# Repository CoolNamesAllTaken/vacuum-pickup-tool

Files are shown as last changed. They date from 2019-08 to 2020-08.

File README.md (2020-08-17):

# vacuum-pickup-tool
Vacuum pickup tool for building SMT boards.

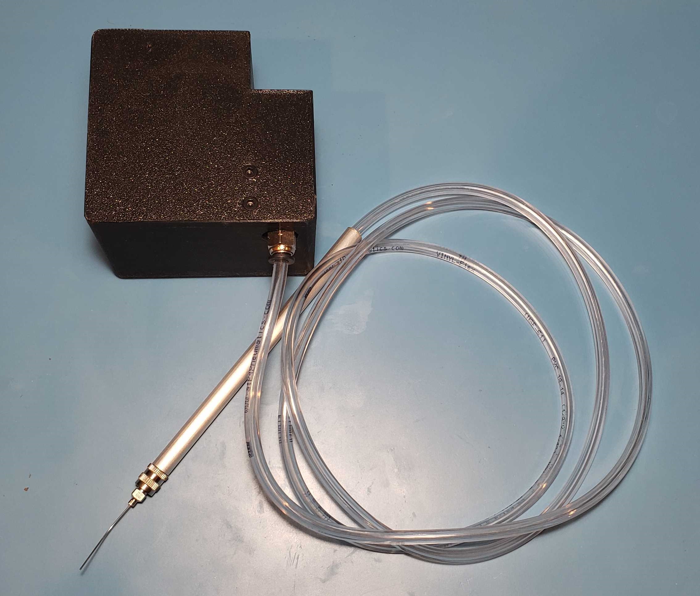
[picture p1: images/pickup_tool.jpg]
Image of fully assembled system


## Overview and Description
The Vacuum Pickup Tool is designed to facilitate manual pick-and-place of SMD components onto PCBs, offering faster cycle time than tweezers, since components can be picked directly from their tape.
It consists of a 3d printed case (powered by a 12V barrel jack), a foot pedal (connected to the case by way of a 3.5mm audio cable), and the tool itself (connected to the case by a PVC vacuum tubing).
The "pencil" terminates in a [Luer lock connector](https://en.wikipedia.org/wiki/Luer_taper), a common standard for affixing needles to syringes.

## Parts List
* 1x [12V NC Solenoid Valve](https://www.amazon.com/gp/product/B07BGXMG7H)
* 1x [12V Brushless Vacuum Pump](https://www.ebay.com/itm/US-Stock-Parker-12V-Brushless-Dual-Head-Vacuum-Pump-Diaphragm-Pump-DIY-Air-Pump/392156385546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)
* 1x [Male Luer Lock to 3mm or 1/8" Hose Barb Adapter](https://www.ebay.com/itm/Metal-Male-Luer-Lock-Syringe-Fitting-to-3mm-or-1-8-Barb-Hose-ID-43/202463602776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)
* 1x [1/6" Hose Barb Tee Fitting](https://www.amazon.com/gp/product/B017UXJ3VG)
* 1x [3/8in Diameter x 12in Aluminum Tube](https://www.ebay.com/itm/K-S-3-8-in-Dia-x-12-in-L-Aluminum-Tube-Round-/383055055746?hash=item592fdc4b82)
* 1x [12V 2-Position 3-Way Solenoid Valve](https://www.amazon.com/uxcell-Miniature-Solenoid-Valve-Positions/dp/B07WS93PCV)
* 1x [12V 1A Power Supply](https://www.amazon.com/gp/product/B00FEOB4EI)
* 1x [Push to Connect Air Hose Fitting](https://www.amazon.com/gp/product/B07H8KPL2W)
* 1x [1/8" ID 1/4" OD Vinyl-Flex Tubing](https://www.amazon.com/gp/product/B00E6BCV0G/ref=ppx_yo_dt_b_asin_title_o01_s02?ie=UTF8&psc=1)
* 1x [Momentary Foot Switch Pedal](https://www.amazon.com/Linemaster-T-91-S-Treadlite-Electrical-Momentary/dp/B002P4XREA)
* 1x [Male to Male 8ft 1/8" Stereo Audio Cable](https://www.amazon.com/AmazonBasics-Stereo-Audio-Cable-Meters/dp/B00NO73Q84)
* 1x [Arduino Nano Clone](https://www.amazon.com/ELEGOO-Arduino-ATmega328P-Without-Compatible/dp/B0713XK923)
* 1x [Adjustable Buck Converter](https://www.amazon.com/Ultra-MP1584EN-Converter-Adjustable-Module/dp/B07SJFTD7F)
* 1x [12V 1A Power Supply (5.5x2.1mm Barrel Jack)](https://www.amazon.com/gp/product/B00FEOB4EI)

## Important Note
The pictures are of an older version of this tool, which has a slightly different PCB that required some extra wire finagling. The air cabling is exactly the same, as are the placements of each part.

## Step 1: Assemble and mount the PCB:
1. Solder all surface mount componenets. In general, going from smallest to largest is advisable so you don't have larger componenets blocking your iron's access to smaller nearby pads.
Keep in mind that diodes and LEDs have polarity! Refer to the pictures or the schematic to see the correct orientation.
2. Solder the male 2pos JST-PH connectors to the board, as well as the barrel jack. Be careful that the JST connectors are in the correct orientation (i.e. the red wire crimped in the female will correspond with the positive side when they are connected.)
3. Set the voltage output of the regulator. We used a bench power supply with alligator clips to supply 12V and a voltmeter with alligator clip leads to read the output voltage. Turn the on-board screw until the output is 5V. It is important to do this before the regulator and the Nano are soldered to the PCB, otherwise the regulator may provide a voltage that fries the Nano's 5V-tolerant pins before it is properly tuned.
4. Solder male headers on the Nano and the regulator. The easist way to get the headers straight up and aligned on the Nano is to place them in a breadboard. This will NOT work for the regulator, as the distances between its holes are inconsistent with a breadboard's.
5. Solder the Nano and regulator to the board.
6. Mount the PCB to the case with four M3 screws and nuts.
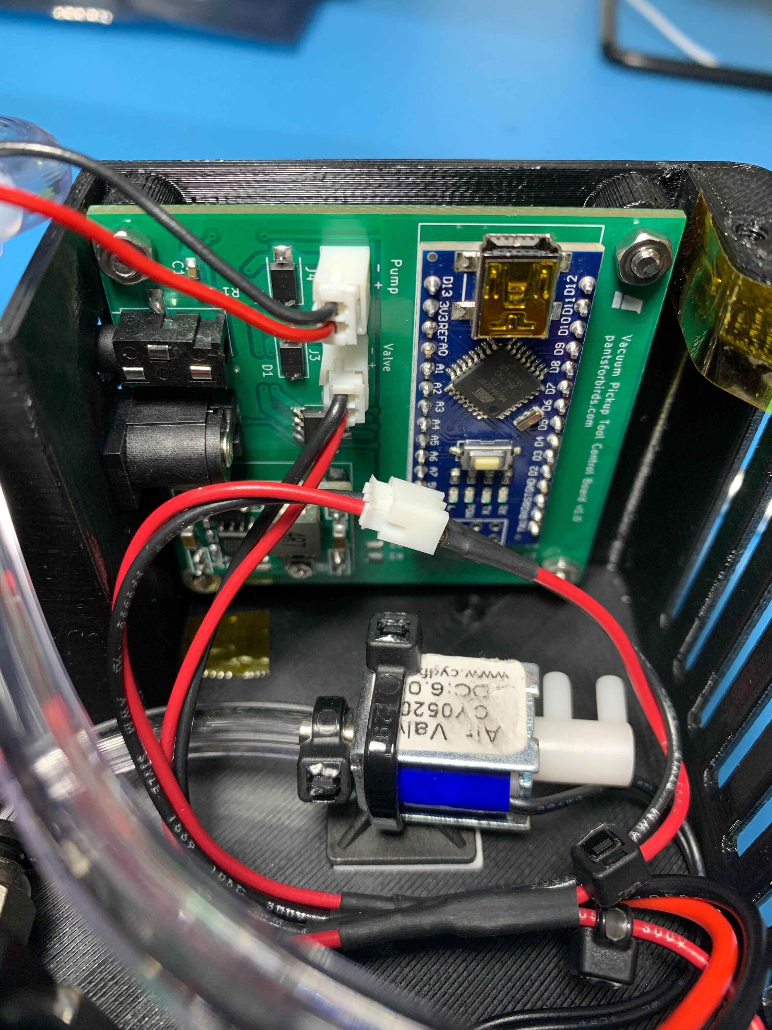
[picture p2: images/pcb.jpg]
Completed PCB


## Step 2: Connect the vacuum pump and solenoids:
1. Crimp and affix a female 2pos JST-PH connector to the leads of the vacuum pump. An Engineer PA-09 crimper can be used for this.
2. Crimp and affix a female 2pos JST-PH connector to the leads of each solenoid.
3. Remove the red "hats" from the vacuum pump.
4. Use two short M4 screws to affix the vacuum pump to the top plate of the case.
5. Place one square nut in each of the slots in each top corner of the case. 
6. Screw in a Push-to-Connect Tube Fitting to each of the three holes in the larger solenoid valve. Use a wrench to get them tight, but it is normal for 3ish threads to still extend outside of the hole when it is fully in.
9. Using the tubing and a T-fitting, connect the tubing as shown in the pictures. Leave enough "slack" so that the top (to which the vacuum pump is attached) can be removed without disconnecting the tubing.
8. Use 2 short M4 screws to affix the large solenoid to the bottom of the case.
9. Use a zip tie and a zip tie mount to affix the small solenoid to the bottom of the case.
10. Plug the female JST connectors into the PCB.
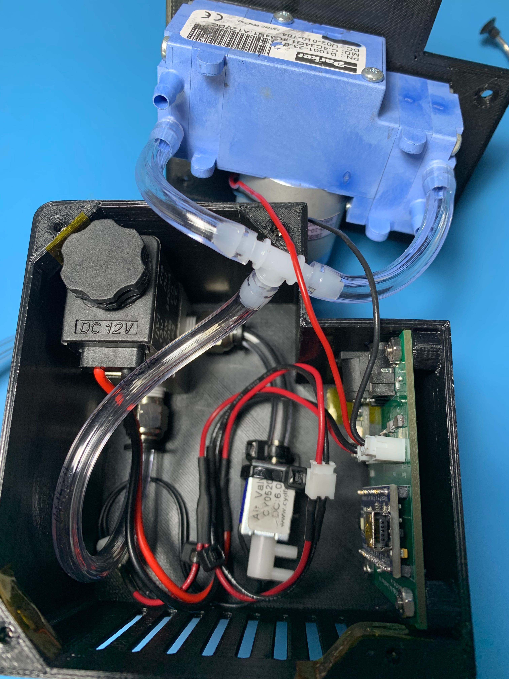
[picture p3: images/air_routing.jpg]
Vacuum pump and solenoids installed


## Step 3: Construct and connect the "pencil":
1. Cut the aluminum tube in half, since we want a 6in length. One way to cut it is by placing half in a vise and cutting with a hacksaw, then deburring and filing the rough edges.
2. Cut a long length of the vinyl tubing and feed it through the aluiminum tube.
3. Attach the Luer Lock adapter, and use Kapton tape to slightly increase the diameter of the front of the tube (over the Luer Lock adapter barb) until it makes a nice press fit into the tube.
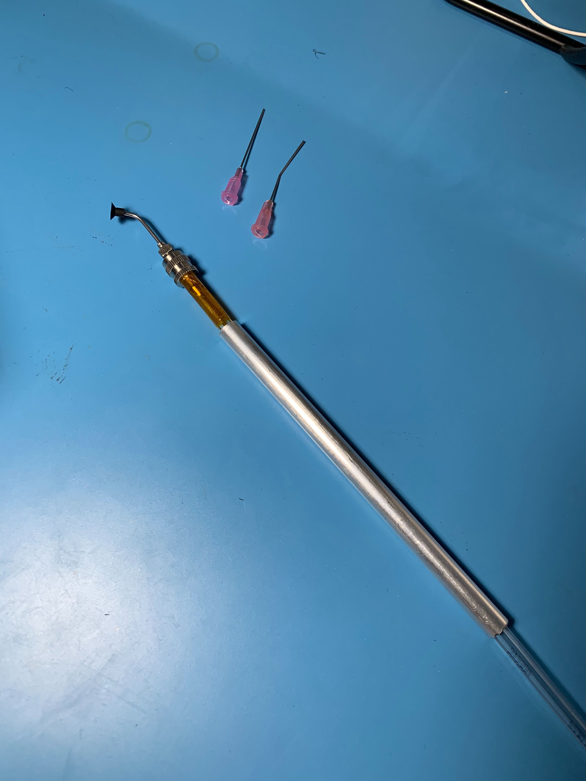
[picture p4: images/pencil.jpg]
Partially assembled pencil, showing Kapton tape that will create a press fit against the aluminum tube


## Step 4: Wire the foot pedal
1. Chop off the connector from one end of the 3.5mm audio cable. Strip ~1in of the outer cable insulation and ~0.3in of the insulation on each of the 3 inner cables.
2. Use a multimeter to map each internal cable to the sleeve, ring, and tip of the other end's connector. Chop off the wire corresponding to the sleeve; it is unneeded.
3. Unscrew the two side screws of the foot pedal to separate the two main pieces. Take out the plastic insert protecting the internal limit switch.
4. Loosen the two back screws to allow the cable through. Of the two remaining wires, solder one to the Common terminal of the limit switch, and the other to the Normally Open (NO) terminal. It may help to remove the limit switch when doing this. If you have the correct size of quick-connect spade terminals, these could be used to attach wires to the switch instead of soldering.
5. Replace the protective plastic, tighten the two back screws to provide strain relief on the incoming cable, then reattach the sides to each other with the side screws.

## Step 5: Build and flash the code:
1. Download and install Microsoft VSCode and the PlatformIO IDE extension following instructions [here](https://platformio.org/install/ide?install=vscode)
2. In the PlatformIO IDE, click Projects, then Add Existing, and navigate to the `src/vacuum_pickup_tool` directory.
3. In the terminal part of the IDE, run `platformio lib install PinChangeInterrupt`.
4. Plug in the Nano with a USB mini cable, and click the Upload arrow on the bottom bar.
5. If the Upload fails, it may be because different Nano clones use different bootloader versions. To try the other version, go to Projects then click the Configure button next to the Vacuum Pickup Tool project. Scroll down to board and change `nanoatmega328` to `nanoatmega328new`, then try again.

## Step 6: Putting it all together:
1. Plug in the 12V power, the audio cable, and the tubing from the "pencil".
2. When the power is inserted, red LEDs should be on inside the case. When the foot pedal is depressed, the vacuum will activate and a green LED should show inside the case.
3. After releasing the foot pedal, the green LED will turn off but the vacuum pump will remain on for a short period of time, so that if you're picking multiple parts in quick succession you don't have to wait for it to start up each time.

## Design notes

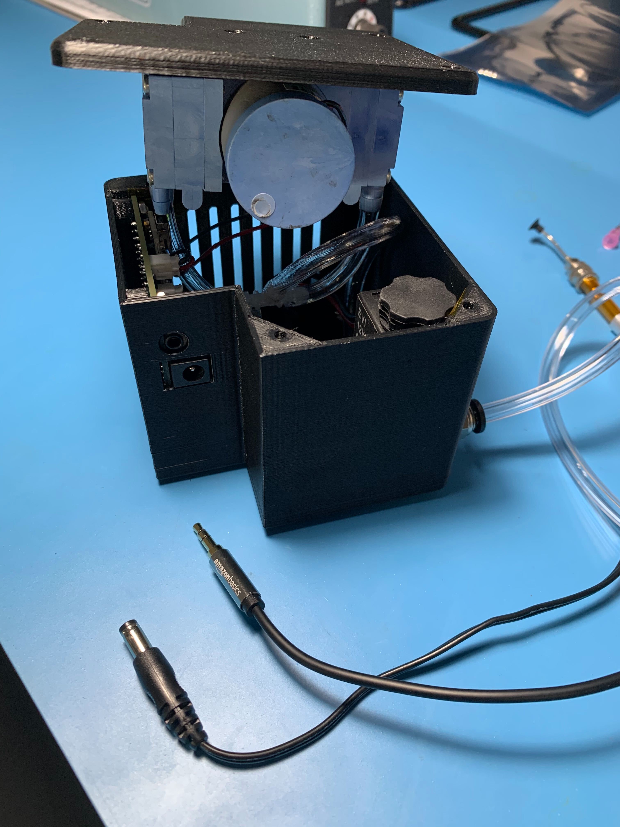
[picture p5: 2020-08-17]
images/power_and_trigger_inputs.jpg

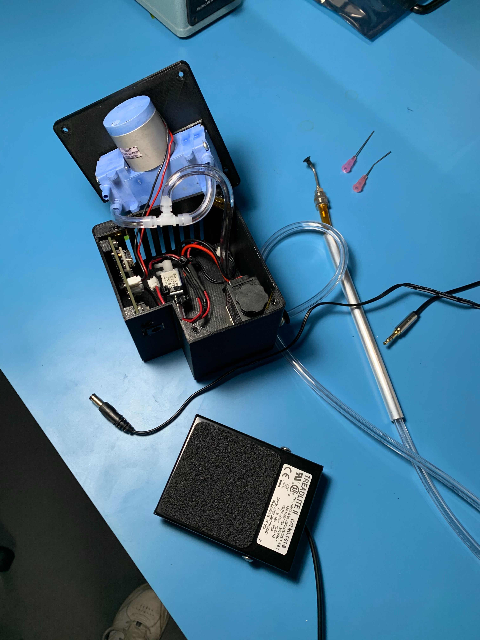
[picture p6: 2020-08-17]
images/entire_system.jpg

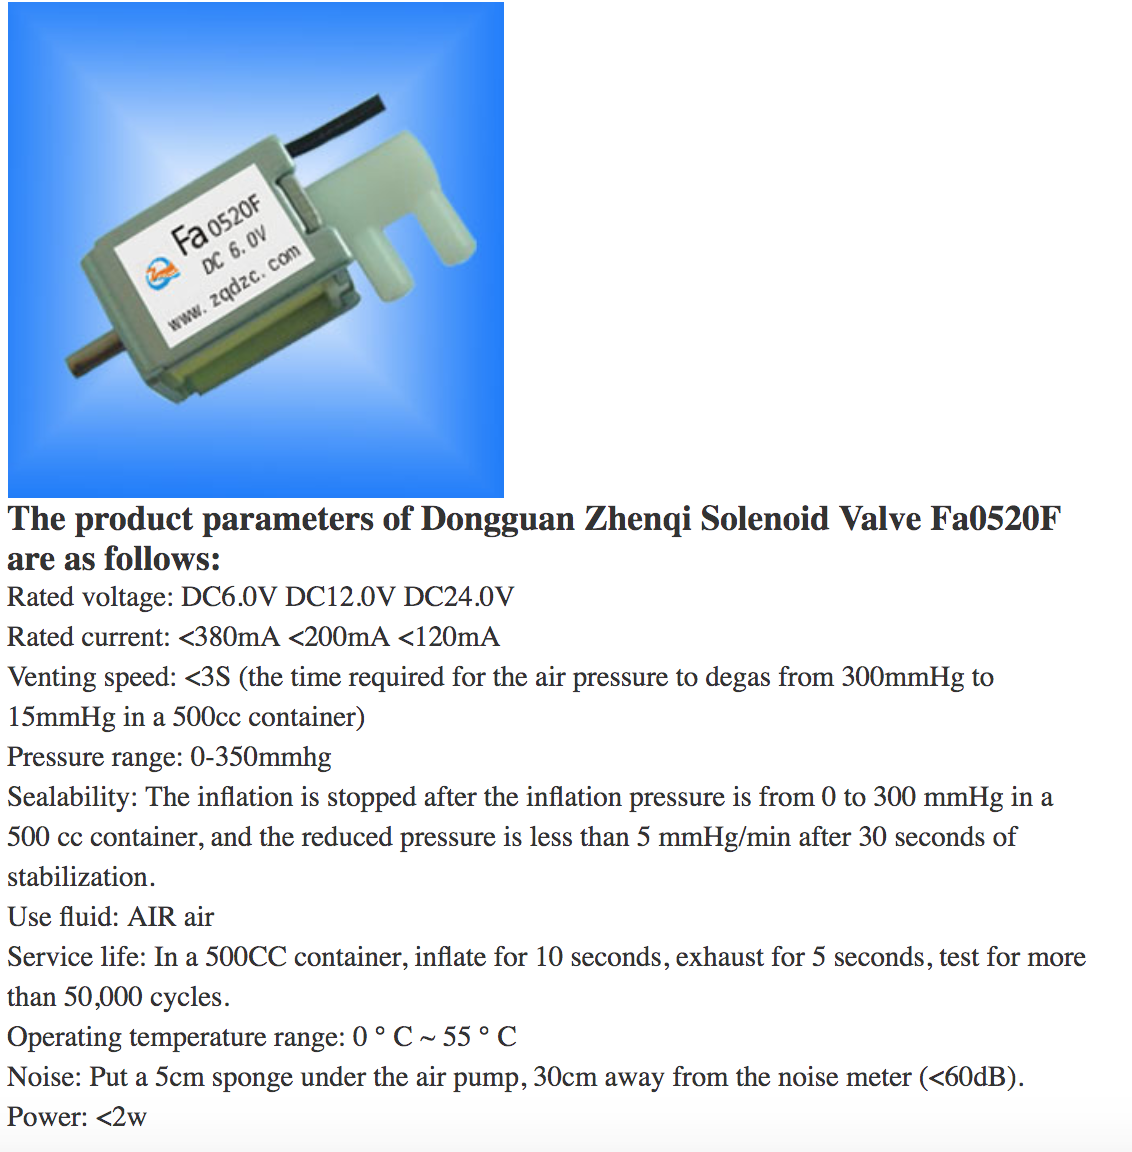
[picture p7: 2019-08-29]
datasheets/Screen Shot 2019-08-22 at 11.06.53 PM.png

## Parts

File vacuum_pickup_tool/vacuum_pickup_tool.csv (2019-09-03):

Reference | Quantity | Value | Footprint | Datasheet | MPN
A1 | 1 | Arduino_Nano_v3.x | lib_fp:Arduino_Nano | http://www.mouser.com/pdfdocs/Gravitech_Arduino_Nano3_0.pdf
C1 | 1 | 0.1uF | Capacitor_SMD:C_0603_1608Metric | ~ | 0603B104K500NT
D1 D4 | 2 | 40V 5A | Diode_SMD:D_SMA | https://datasheet.lcsc.com/szlcsc/1903061001_MDD-Jiangsu-Yutai-Elec-SS54_C22452.pdf | SS54
D2 | 1 | LED_RED | LED_SMD:LED_0603_1608Metric | https://datasheet.lcsc.com/szlcsc/Foshan-NationStar-Optoelectronics-FC-DA1608HRK-620D_C84263.pdf | FC-DA1608HRK-620D
D3 | 1 | LED_GREEN | LED_SMD:LED_0603_1608Metric | https://datasheet.lcsc.com/szlcsc/Foshan-NationStar-Optoelectronics-FC-DA1608UGK-520D10_C84267.pdf | FC-DA1608UGK-520D10
H1 H2 H3 H4 | 4 | MountingHole | MountingHole:MountingHole_3.2mm_M3 | ~
J1 | 1 | Barrel_Jack | lib_fp:SOFNG_DC005-T20 | https://datasheet.lcsc.com/szlcsc/1908270930_Boom-Precision-Elec-DC-005-5-5-2-0MM_C16214.pdf | DC005-T20
J2 | 1 | AudioJack3 | lib_fp:Boom_PJ-320B | https://datasheet.lcsc.com/szlcsc/Boom-Precision-Elec-PJ-320B_C18594.pdf | PJ-320B
J3 J4 | 2 | JST_PH_01x02_Male | Connector_JST:JST_PH_B2B-PH-K_1x02_P2.00mm_Vertical | ~ | B2B-PH-K-S(LF)(SN)
R1 | 1 | 10k | Resistor_SMD:R_0603_1608Metric | ~ | RC0603JR-0710KL
R2 | 1 | 680R | Resistor_SMD:R_0603_1608Metric | ~ | 0603WAF6800T5E
R3 | 1 | 510R | Resistor_SMD:R_0603_1608Metric | https://datasheet.lcsc.com/szlcsc/YAGEO-RC0603FR-07510RL_C114670.pdf | RC0603FR-07510RL
U1 | 1 | Amazon_Small_Buck | lib_fp:Amazon_Small_Buck | https://www.amazon.com/gp/product/B014Y3OT6Y
U2 | 1 | NCE6005AS | lib_fp:SOP-8_3.76x4.96mm_P1.27mm |  | NCE6005AS

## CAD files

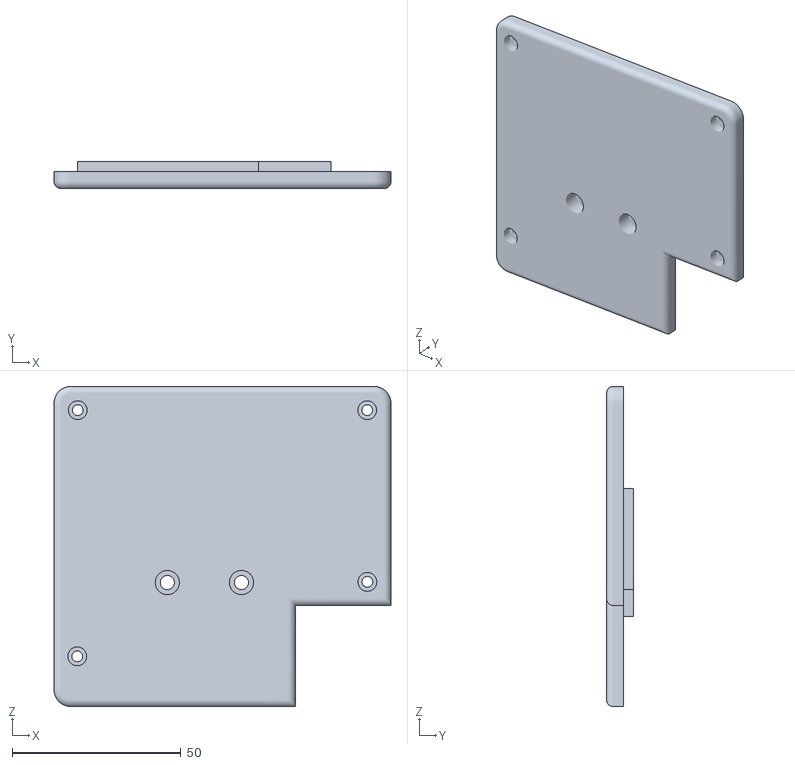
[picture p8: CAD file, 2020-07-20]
stl/pickup_tool_bottom_cover.stl
100.0 x 8.00 x 95.0

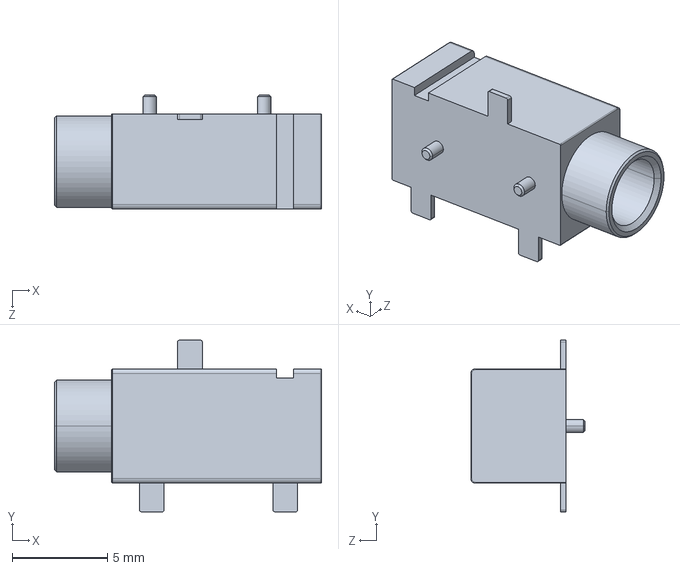
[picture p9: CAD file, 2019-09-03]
vacuum_pickup_tool/lib_3d/PJ-320B.step
14.0 x 9.00 x 6.00 mm

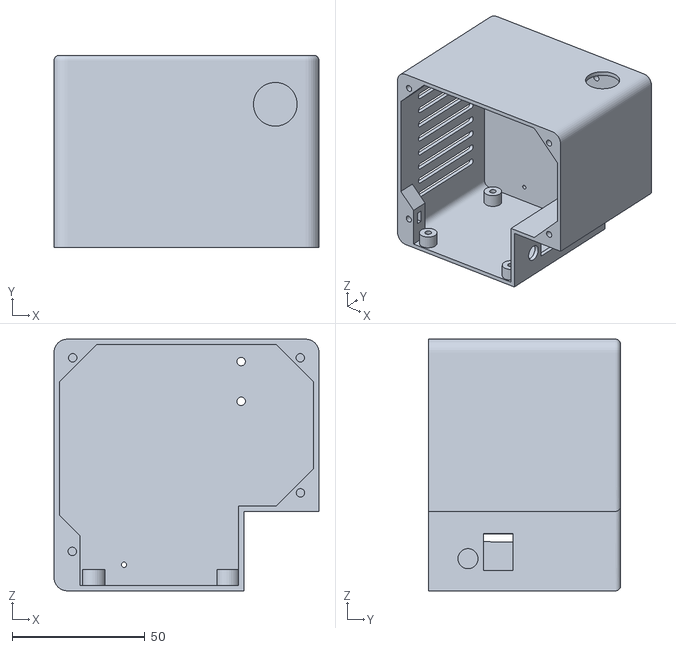
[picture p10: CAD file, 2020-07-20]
stl/pickup_tool_case.stl
100.0 x 72.6 x 95.0

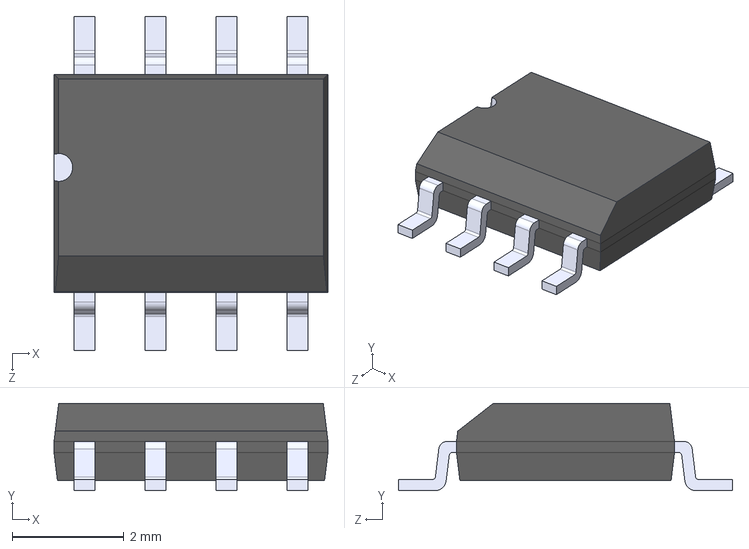
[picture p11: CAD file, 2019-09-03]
vacuum_pickup_tool/lib_3d/SOP-8_3.76x4.96mm_P1.27mm.STEP
4.90 x 1.56 x 5.98 mm
User Library-sop8_model_pin5to8_sop8 x 8
User Library-sop8_model_sop8_body

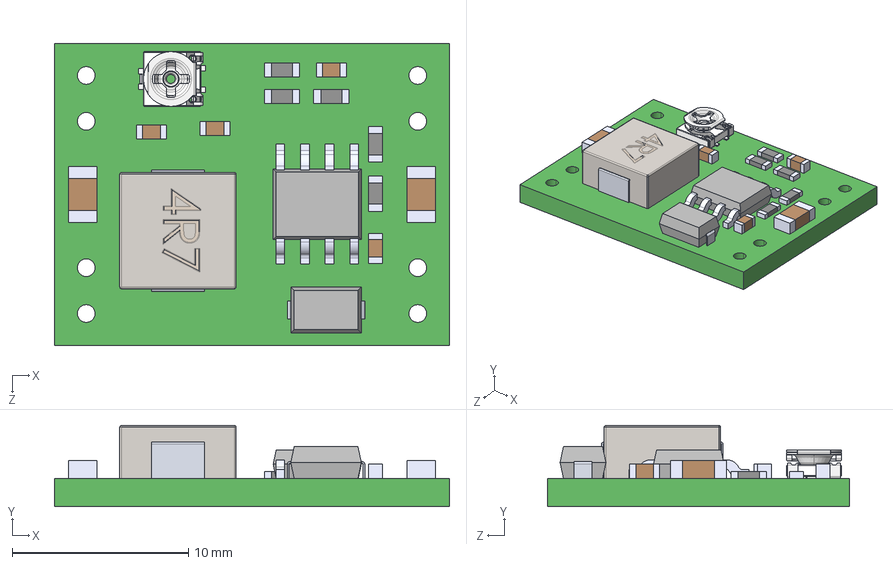
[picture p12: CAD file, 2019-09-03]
vacuum_pickup_tool/lib_3d/Amazon_Small_Buck.STEP
22.4 x 4.60 x 17.1 mm
PCB, DC-DC 4.5-28V to 0.8-20V Output 3A MP1584EN Step Down Buck Converter
MP1584EN CHIP, DC-DC 4.5-28V to 0.8-20V Output 3A MP1584EN Step Down Buck Converter
INDUCTOR, DC-DC 4.5-28V to 0.8-20V Output 3A MP1584EN Step Down Buck Converter
SCHOTTKY DIODE, DC-DC 4.5-28V to 0.8-20V Output 3A MP1584EN Step Down Buck Converter
LARGE SMD CAPACITOR, DC-DC 4.5-28V to 0.8-20V Output 3A MP1584EN Step Down Buck Converter x 2
SMD RESISTOR, 104, DC-DC 4.5-28V to 0.8-20V Output 3A MP1584EN Step Down Buck Converter x 4
SMD RESISTOR, 822, DC-DC 4.5-28V to 0.8-20V Output 3A MP1584EN Step Down Buck Converter
SMALL SMD CAPACITOR, DC-DC 4.5-28V to 0.8-20V Output 3A MP1584EN Step Down Buck Converter x 4
POTENTIOMETER, DC-DC 4.5-28V to 0.8-20V Output 3A MP1584EN Step Down Buck Converter

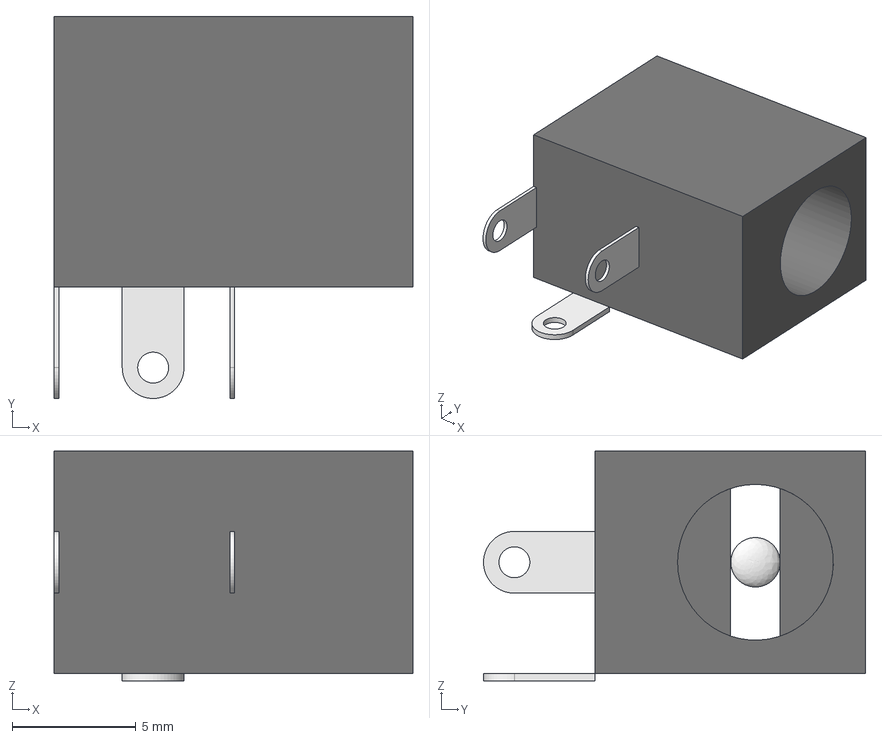
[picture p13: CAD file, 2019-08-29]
vacuum_pickup_tool/lib_3d/DC Jack v2.step
14.5 x 15.4 x 9.30 mm

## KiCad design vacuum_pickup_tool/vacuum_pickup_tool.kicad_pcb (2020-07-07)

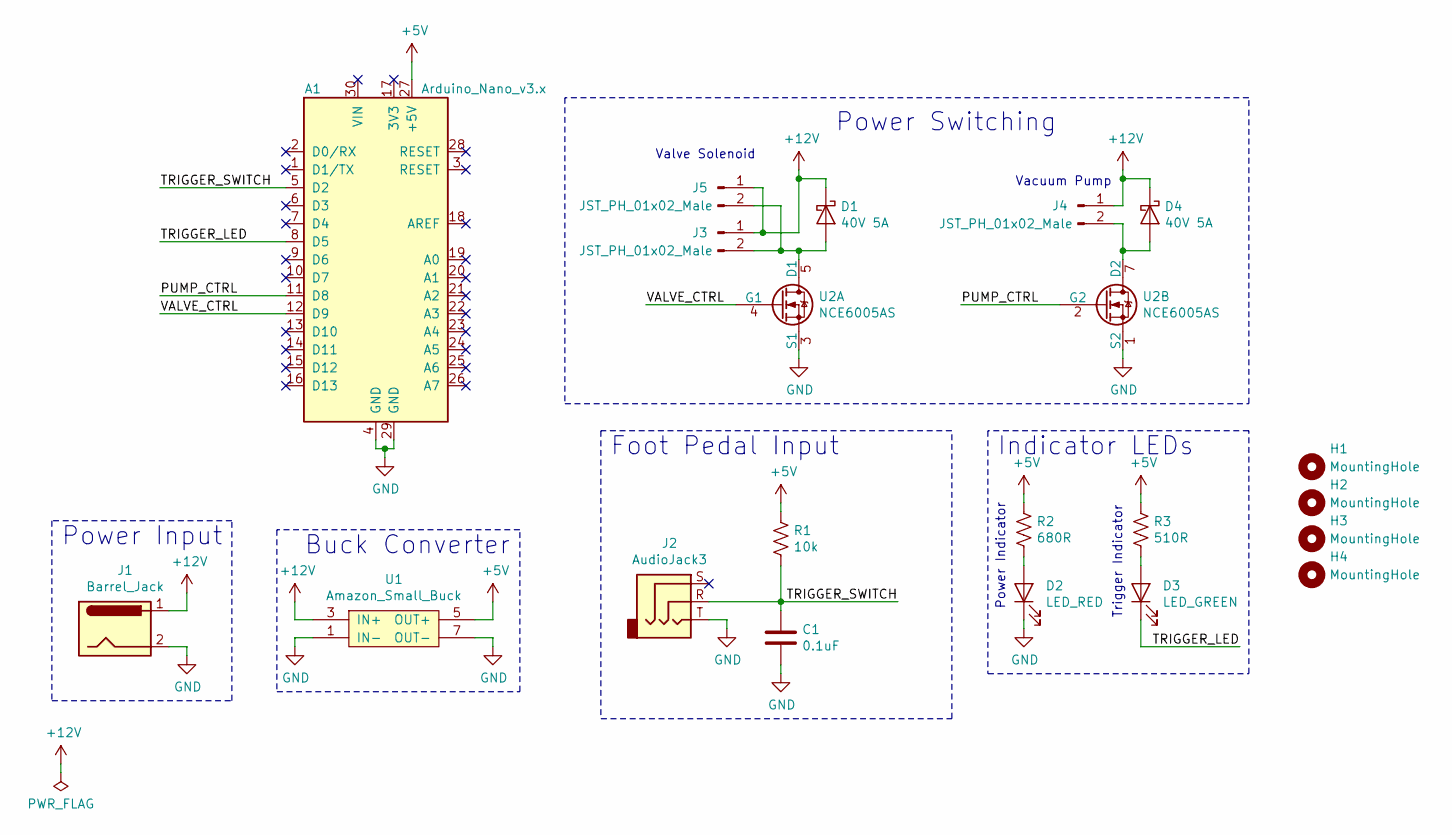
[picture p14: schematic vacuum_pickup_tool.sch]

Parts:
A1: Arduino_Nano_v3.x; Arduino_Nano
C1: 0.1uF; C_0603_1608Metric; MPN 0603B104K500NT
D1, D4: 40V 5A; D_SMA; MPN SS54
D2: LED_RED; LED_0603_1608Metric; MPN FC-DA1608HRK-620D
D3: LED_GREEN; LED_0603_1608Metric; MPN FC-DA1608UGK-520D10
H1, H2, H3, H4: MountingHole; MountingHole_3.2mm_M3
J1: Barrel_Jack; SOFNG_DC005-T20; MPN DC005-T20
J2: AudioJack3; Boom_PJ-320B; MPN PJ-320B
J3, J4, J5: JST_PH_01x02_Male; JST_PH_B2B-PH-K_1x02_P2.00mm_Vertical; MPN B2B-PH-K-S(LF)(SN)
R1: 10k; R_0603_1608Metric; MPN RC0603JR-0710KL
R2: 680R; R_0603_1608Metric; MPN 0603WAF6800T5E
R3: 510R; R_0603_1608Metric; MPN RC0603FR-07510RL
U1: Amazon_Small_Buck
U2: NCE6005AS; SOP-8_3.76x4.96mm_P1.27mm; MPN NCE6005AS

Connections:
+5V: A1.27 (+5V), R1.1, R2.1, R3.1, U1.5 (OUT+), U1.6 (OUT+)
+12V: D1.1 (K), D4.1 (K), J1.1, J3.1, J4.1, J5.1, U1.3 (IN+), U1.4 (IN+)
/PUMP_CTRL: A1.11 (D8), U2.2 (G2)
/TRIGGER_LED: A1.8 (D5), D3.1 (K)
/TRIGGER_SWITCH: A1.5 (D2), C1.1, J2.R, R1.2
/VALVE_CTRL: A1.12 (D9), U2.4 (G1)
GND: A1.4 (GND), A1.29 (GND), C1.2, D2.1 (K), J1.2, J2.T, U1.1 (IN-), U1.2 (IN-), U1.7 (OUT-), U1.8 (OUT-), U2.1 (S2), U2.3 (S1)
unnamed: D1.2 (A), J3.2, J5.2, U2.5 (D1), U2.6 (D1)
unnamed: D2.2 (A), R2.2
unnamed: D3.2 (A), R3.2
unnamed: D4.2 (A), J4.2, U2.7 (D2), U2.8 (D2)

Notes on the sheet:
Valve Solenoid
Vacuum Pump
Power Switching
Buck Converter
Power Input
Foot Pedal Input
Power Indicator
Trigger Indicator
Indicator LEDs

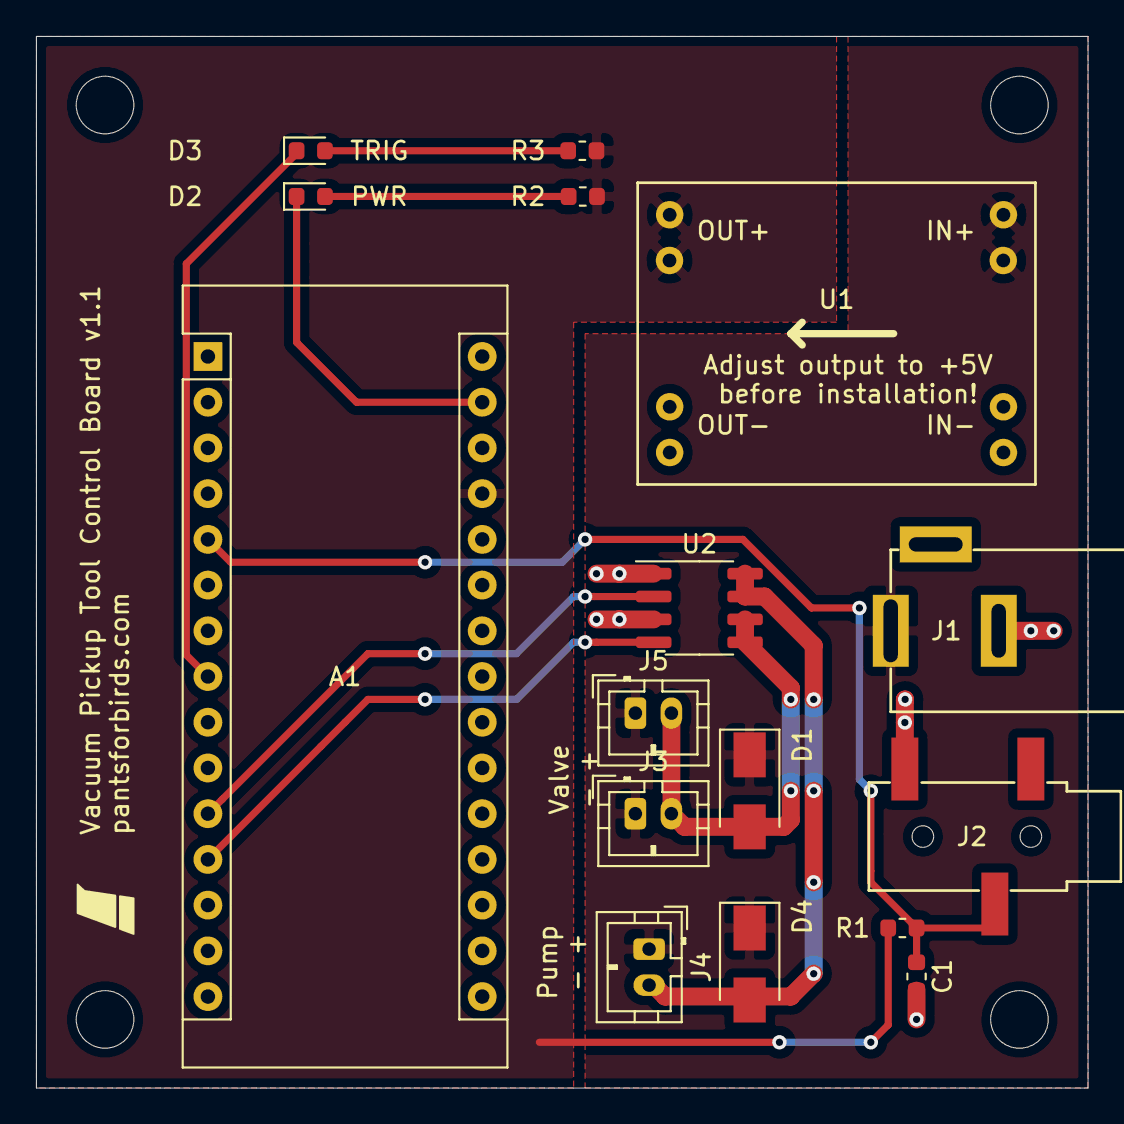
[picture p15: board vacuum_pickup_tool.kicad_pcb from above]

Board: 2 copper layers, 58.4 x 58.4 mm, 20 parts (0 on the bottom side), 11 nets.

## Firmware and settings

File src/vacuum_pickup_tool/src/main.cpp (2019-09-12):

#include <Arduino.h>
#include <PinChangeInterrupt.h>

#define DEBUG

#define TRIGGER_PIN 2
#define TRIGGER_LED_PIN 5
#define PUMP_CTRL_PIN 8
#define VALVE_CTRL_PIN 9

#define VALVE_PWM_DELAY_MS 200 // time after valve trigger until PWMing solenoid
#define VALVE_PWM_DUTY_CYCLE 175 // 0-255, holding current for solenoid valve
#define PUMP_TIMEOUT_MS 5000 // time after last valve trigger that pump turns off

uint32_t last_trigger_time_ms = millis();
bool triggered = false;

void trigger_isr();

void setup() {
  // put your setup code here, to run once:

  #ifdef DEBUG
  Serial.begin(115200);
  #endif

  pinMode(TRIGGER_PIN, INPUT);
  pinMode(TRIGGER_LED_PIN, OUTPUT);
  pinMode(PUMP_CTRL_PIN, OUTPUT);
  pinMode(VALVE_CTRL_PIN, OUTPUT);

  attachPCINT(digitalPinToPCINT(TRIGGER_PIN), trigger_isr, CHANGE);

  digitalWrite(TRIGGER_PIN, LOW);
  digitalWrite(TRIGGER_LED_PIN, HIGH); // inverted
  digitalWrite(PUMP_CTRL_PIN, LOW);
  digitalWrite(VALVE_CTRL_PIN, LOW);
}

void loop() {
  // put your main code here, to run repeatedly:

  if (triggered) {
    // picking up component
    Serial.println("TRIGGERED");
    if (millis() - last_trigger_time_ms > VALVE_PWM_DELAY_MS) {
      // PWM the solenoid for lower holding current
      analogWrite(VALVE_CTRL_PIN, VALVE_PWM_DUTY_CYCLE);
      analogWrite(TRIGGER_LED_PIN, 255 - VALVE_PWM_DUTY_CYCLE);
    } else {
      // solenoid 100% on for initial movement
      digitalWrite(VALVE_CTRL_PIN, HIGH);
      digitalWrite(TRIGGER_LED_PIN, LOW);
    }
  } else {
    // component released
    Serial.println("nah");
    digitalWrite(VALVE_CTRL_PIN, LOW);
    digitalWrite(TRIGGER_LED_PIN, HIGH);

    if (millis() - last_trigger_time_ms > PUMP_TIMEOUT_MS) {
    // turn off pump
    digitalWrite(PUMP_CTRL_PIN, LOW);
  }
  }
}

void trigger_isr() {
  uint8_t trigger = getPinChangeInterruptTrigger(digitalPinToPCINT(TRIGGER_PIN));
  last_trigger_time_ms = millis();

  if (trigger == RISING) {
    // rising edge
    triggered = false;
  } else {
    // falling edge
    triggered = true;
    digitalWrite(PUMP_CTRL_PIN, HIGH);
  }
}

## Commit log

2019-08-29 Make v1.0 of board
    [Amazon_Small_Buck.STEP, DC Jack v2.step, PJ-320B.step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]
2019-09-03 Make v1.0
    [Amazon_Small_Buck.STEP, PJ-320B.step, SOP-8_3.76x4.96mm_P1.27mm.STEP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]
2019-09-12 Make code for v1.0
    [vacuum_pickup_tool.sch]
2020-07-07 Add hella files and README parts
    [vacuum_pickup_tool-B_Cu.gbr, vacuum_pickup_tool-B_Mask.gbr, vacuum_pickup_tool-B_Paste.gbr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]
2020-07-20 Add stls for 3D printed parts
    [pickup_tool_bottom_cover.stl, pickup_tool_case.stl]
